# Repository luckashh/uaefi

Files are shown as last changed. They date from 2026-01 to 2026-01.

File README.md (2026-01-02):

# Ultra Affordable EFI

🟢[$175 base model rusEFI store](https://www.shop.rusefi.com/shop/p/uaefi-ultra-affordable-efi)🟢

## Community Support

🔴Community support ONLY 🔴 https://www.facebook.com/groups/rusEfi 🔴 [Discord](https://github.com/rusefi/rusefi/wiki/Discord)🔴 [Commercial Support](https://www.shop.rusefi.com/shop/p/details-about-rusefi-ecu-technical-support) 🔴

## Technical Details

Open Source KiCAD hardware powered by [Hellen-One](https://github.com/andreika-git/hellen-one)

Powered by [rusEFI firmware](https://github.com/rusefi/rusefi)

[User Documentation](https://github.com/rusefi/rusefi/wiki/uaEFI)





## MCU options

1mb of flash is _required_.

One day we shall try https://jlcpcb.com/partdetail/Stmicroelectronics-STM32F427VIT6%2FC57097#EC or https://jlcpcb.com/partdetail/Stmicroelectronics-STM32F437VIT7%2FC1338578#EC

## rusEFI Store

https://www.shop.rusefi.com/shop/p/uaefi-ultra-affordable-efi

## HOWTO JLCPCB

You would need three files from ``boards/uaefi-a/board`` folder to place your JLCPB Assembly order: gerber.zip BOM-JLC.csv and CPL.csv

### Q: having trouble with opening uaefi board project. library path seems ok, i do not know how to solve missing modules issue

A: missing modules are closed source. they are filled in by github magic
github magic combines gerbers and spits out a complete bom/pcl/new gerbers to upload to jlc/friends. See https://github.com/rusefi/hellen-one/tree/master?tab=readme-ov-file#tldr for more info

### Q: Magic modules? How do I see schematics of those?

A: https://github.com/rusefi/hellen-one has full documentation for each module

### Q: Something wrong with BOM?

A: Nope, that's normal nothing to worry about click 'Continue'.



### Q: how do I get more RAM for Lua?

A: fabricate with STM32F42xVI firmware would defect extra RAM and give you extra Lua. Once your script does not fit into STM32F42xVI it's F7 time or help us leverage F413.

### Q: I've place an order with JLCPCB and I see scary looking wrong orientation?

A: that's expected. See [boards/uaefi-c/board](boards/uaefi-c/board) ``Original*.png`` files and ``Produce*.png`` after JLCPCB manual review process.

## Bluetooth power issue fix

It was found that board with installed BT module may be affected by power issue.

During power on BT module consume too much inrush current on 3.3V line causing 3.3V drop below MCU reset hreshold. This may lead to unstable start or infinity reset loop.

To fix this please install additional capacitors to 5V and 3.3V powerlines.

Polarized electrolytic capacitors with at least 10V rating and extended temperature range are recommended. Tantalum and solid electrolytic capacitors are also suitable.

**Please carefully follow illustrated polarity.**

33..47uF should be added to 5V powerrail. [This](https://www.digikey.com/en/products/detail/w%C3%BCrth-elektronik/860020372004/5727028) or [this](https://www.digikey.com/en/products/detail/w%C3%BCrth-elektronik/860080372001/5727224) or [any of these](https://www.digikey.com/en/products/filter/aluminum-electrolytic-capacitors/58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).



And 220..470uF should be added to 3.3V powerrail. [This](https://www.digikey.com/en/products/detail/w%C3%BCrth-elektronik/860010273011/5726952) or [this](https://www.digikey.com/en/products/detail/w%C3%BCrth-elektronik/860020273011/5727148) or [any of these](https://www.digikey.com/en/products/filter/aluminum-electrolytic-capacitors/58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).



## HOWTO EGT chip

This board has a placeholder for MAX31855 (or MAX6675) termocouple-to-digital chip. **This chip is not populated by default!**

Screenshot from 2025-09-26 11-15-15

D8 is **optional** ESD protection and also is not populated by default. You need to solder U4 only, D8 is optional. All passive components are already populated.

**MAX31855** works without addtional modification.

For **MAX6675** connect EGT- to GNDA either on J2 "C" connector or just short C28 (replace with 0R).

Screenshot from 2025-09-26 11-19-41

## [EXPERIMENTAL] How to make MAX9924 work with low tooth count trigger wheel

In some cases user may need two VR inputs on UAEFI and both trigger wheels are low-tooth count.

In default configuration MAX9924 does not work with low count trigger wheels because of its "adaptive peak threshold" and its watchdog.

Screenshot from 2025-10-12 16-58-30

On UAEFI MAX9924 is configured in **A2 mode**.

Screenshot from 2025-10-12 16-59-49

**B mode** allow use of MAX9924 with low count trigger wheels. But external Bias and Thresholt voltages should be allpied. Both can be sources from UAEFI Discrete VR module.

List of modifications:
1. pin 6: ZERO_EN connect to VCC instead of GND.
2. pin 4: supply 2.5 V instead of GND
3. pin 8: EXT, supply external threshold voltage

Pins 4 and 6 needs to be lifted from PCB to be disconnected from GND. Pin 8 initially is not connected to any circuit.

Use hot air gun to de-solder whole chip. Then twist pins 4 and 6 up so both do not touch PCB. Then solder chip back to PCB

Now use thin wire to connect:
1. pin 6 to pin 10 of the same chip.
2. pin 4 to **Vref** at R769 + C754. See file:///home/work/rusefi/docs/uaefi-d-ibom.html for its locations
3. pin 8 to **thresh_high** at U756 pin 1. See file:///home/work/rusefi/docs/uaefi-d-ibom.html for its locations



Now MAX9924 VR input uses same threshold vs RPM settings that is set for Descrete VR input. And it is cabable to work with low tooth count trigger wheels without noise issues.

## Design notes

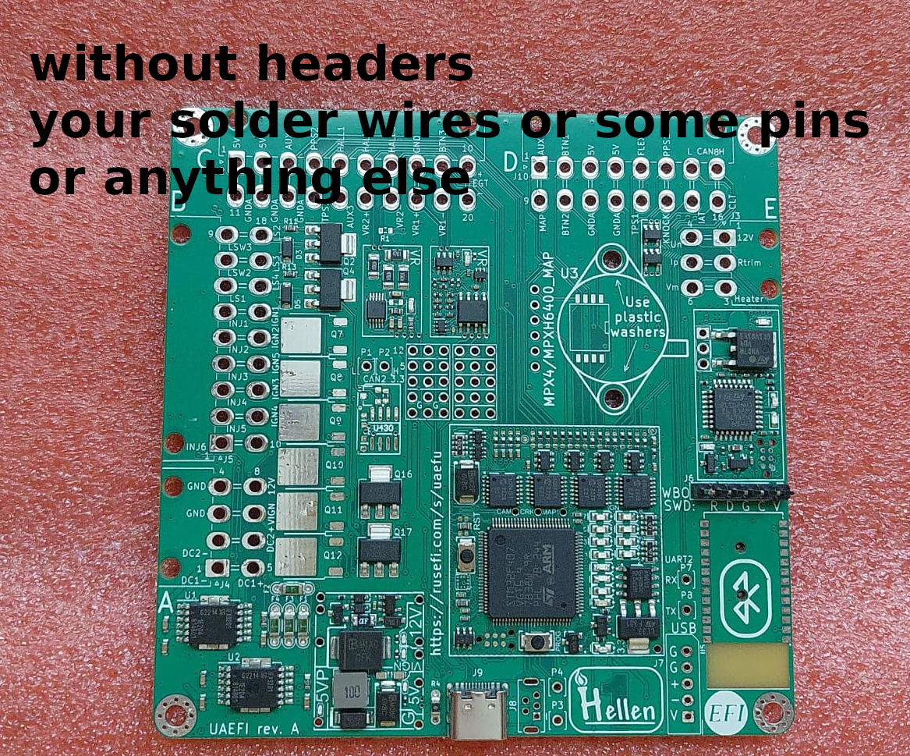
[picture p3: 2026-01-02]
docs/without-headers.png

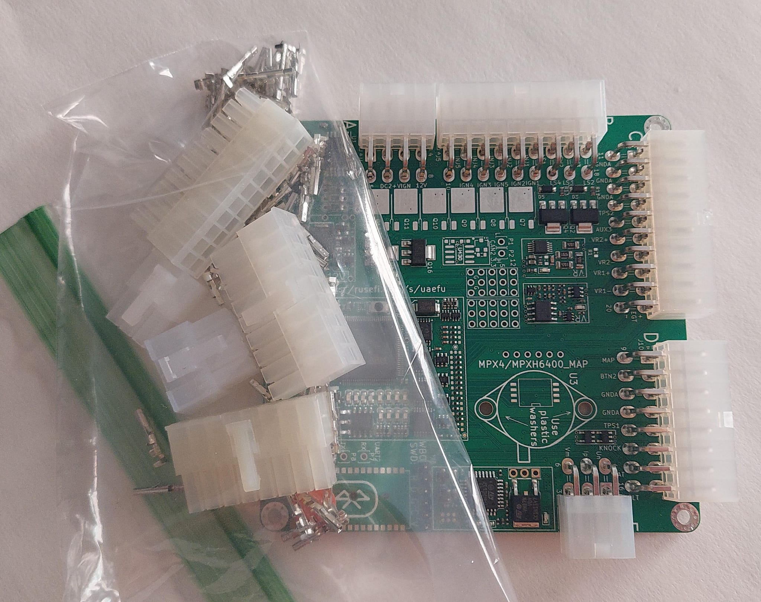
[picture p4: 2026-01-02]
docs/with-crimp-kit.jpg

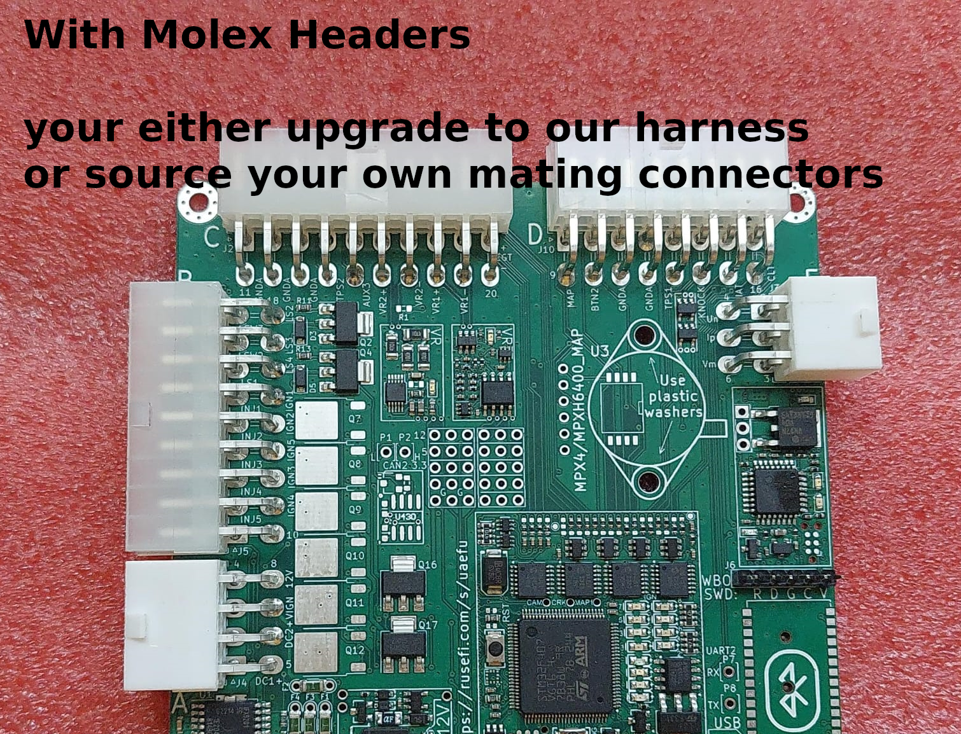
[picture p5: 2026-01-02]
docs/with-headers.png

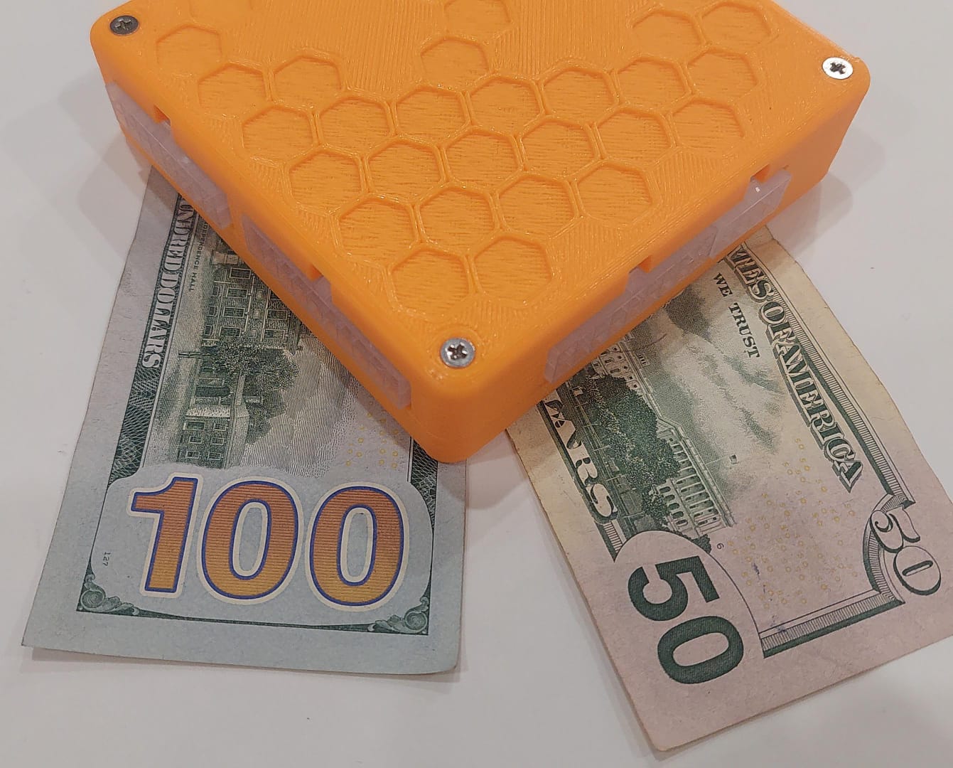
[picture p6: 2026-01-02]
docs/orange-150.jpg

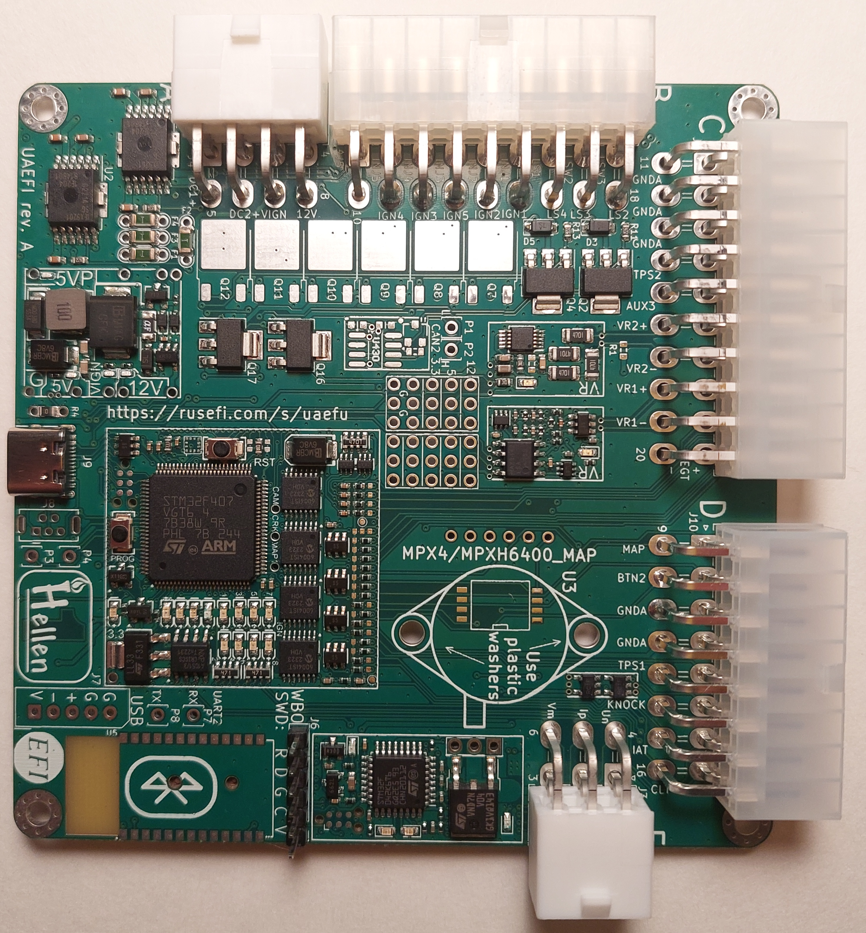
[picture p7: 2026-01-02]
docs/uaefi-a-top-high-res.jpg

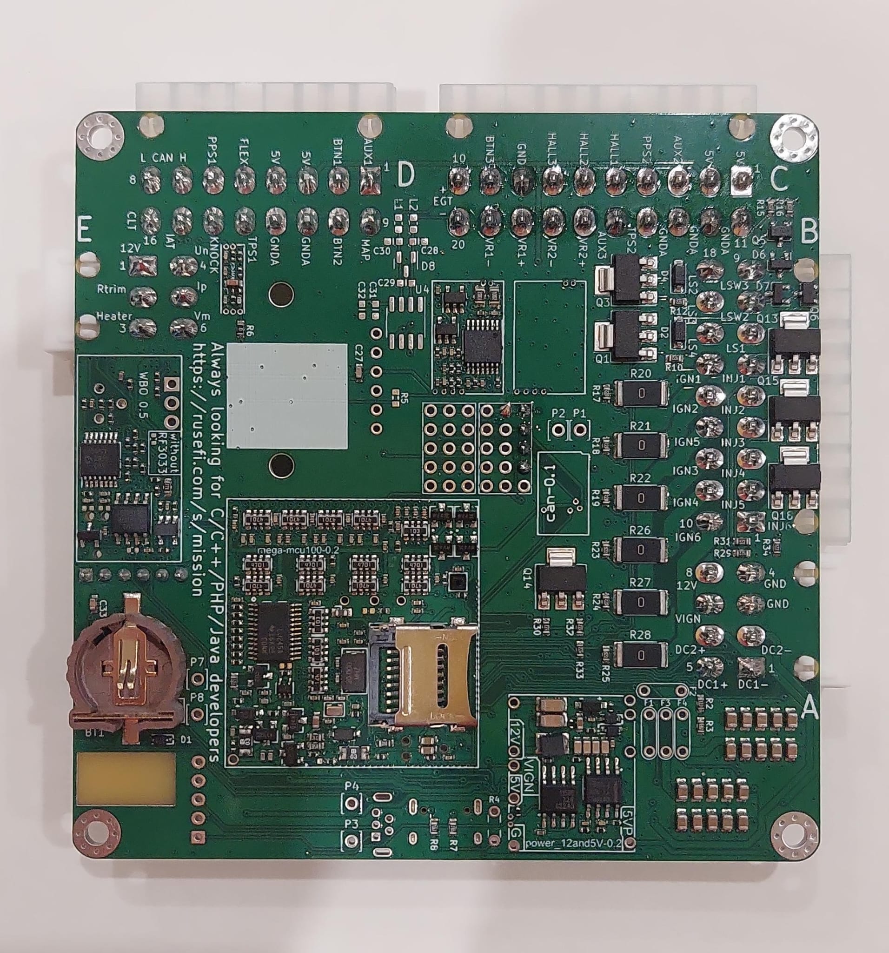
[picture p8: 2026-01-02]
docs/base-bottom.jpg

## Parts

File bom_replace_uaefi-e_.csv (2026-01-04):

# remove +5V pull-ups from SPI1, because we use it with +3.3v accelerometer
R103,
R105,
# remove jumper resistor connecting BOOT1 with A22 input line, because we use STM32F4
R131,
#CAN wakeup disabled, O2S input enabled
R145,
#PWR_EN not used as GPIO
R142,
# DC-DC Inductor
L421,"MWSA0503S-100MT","MWSA0503","C408412"
L420,"NLCV32T-2R2M-EF","L1210","C250227"
# fuses
F410,"nSMD050-24V","SMD1206","C70076"
# replacement not needed "F1,F2,F3,F4","5A","F1206","C553924"
# TLS115
U411,"TLS115B0EJXUMA1","PG-DSO-8","C3747428"
#MAX9142
U754,"TLV3202AIDR","SO8","C129325"
# cost reduction
U106,
# DNP BLUETOOTH JDY
U5,
# more proper part and shelf
"U1,U2","TLE9201SG","Infineon_PG-DSO-12-11","C2653438"
# EGT System restored
"U4","MAX31855KASA","SO-8","C50438"
"D8","MMSZ5231B","SOD-123","C13710"
"C603","33n","C0402","C106862"
#Knock capacitor
"C471","3.3n","C0402","C107028"
# max9924
U771,"MAX9924UAUB+T","MSOP10","C5145181"
# STM32F407VGT6 is very cheap
U105,"STM32F407VGT6","LQFP100","C12345"
# CAN2 restored
"U430","SIT1050T/E","SOIC-8","C12271"
"D430","PESD2CAN","SOT-23","C14986"
"R430","120","R0603","C22775"
"C430,C431","100n","C0603","C14663"
#20MHz crystal
# replacement not needed Y102,"TXM20M0002503LFBEO00T","SMD5032-2P","C362485"
#SD Card
J100,"TF-014-H16","SMD","C125814"
#board ID capacitor shortage
"C123,C133","1u","C0603","C14664"
R609,"61.9","R0603","C321964"
#VNLD5090
"U6,U7,U8,U9,U10,U11","VNLD5090","SO-8","C222209"
#mux
"U755,U756","WAS3157B-6","SOT-363","C213161"
#78 IGN buf switch to SN74LXCH8T245PWR
U103,"SN74LXCH8T245PWR","TSSOP-24","C2918963"
#79 RTC battery drain
D107,
# availability and cost reduction
J2,"5569-20A2","2x10P 2 4.2mm Female pin 4.2mm","C2845795"
J3,"5569-06A2","2x3P 2 4.2mm 4.2mm 3 Brass Push-Pull","C19188572"
J4,"5569-08A2","2x4P 2 Tin 4.2mm Female 4.2mm","C388760"
J5,"5569-18A2","2x9P 2 4.2mm Female 4.2mm 9 Right-Angle","C725776"
J10,"39301160","02x08_4.2mm","C5355564"
# Q1 Selection (Verified for 2026)
# ZXMS6005SGTA is the best cost/performance ratio for 2A loads.
# VNL5160 is not a direct drop-in replacement due to different pinout/logic.
"Q1","ZXMS6005SGTA","SOT-223","C174042"
# cost
"D411","PSM712-LF","SOT-23","C5180294"
#LEDs
"D106","YELLOW_LED","LED0603","C165983"
"D751,D771,D601,D104,D108","GREEN_LED","LED0603","C965804"
"D602,D105,D109,D110,D111,D112,D113,D114,D115,D116","BLUE_LED","LED0603","C497940"
"LED1, LED2, LED3, LED4","BLUE_LED","LED0402","C434447"
# same board ID as rev A for now!
#include hellen-one/board_id/generated/board_id_uaefi-a.csv
#include bom_pullups_uaefi-e.csv

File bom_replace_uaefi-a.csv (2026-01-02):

# remove +5V pull-ups from SPI1, because we use it with +3.3v accelerometer
R103,
R105,
# remove jumper resistor connecting BOOT1 with A22 input line, because we use STM32F4
R131,
#CAN wakeup disabled, O2S input enabled
R145,
#PWR_EN not used as GPIO
R142,
# DC-DC Inductor
L421,"MWSA0503S-100MT","MWSA0503","C408412"
# fuses
F410,"nSMD050-24V","SMD1206","C70076"
# TLS115
U411,"TLS115B0EJXUMA1","PG-DSO-8","C3743696"
# no software for accelerometer
U106,
# STM32F407VGT6 is very cheap
U105,"STM32F407VGT6","LQFP100","C12345"
#without CAN2
"C430,C431,D430,R430,U430",
#20MHz crystal
Y102,"TXM20M0002503LFBEO00T","SMD5032-2P","C362485"
#SD Card
J100,"TF-014-H16","SMD","C125814"
#board ID capacitor shortage
C133,"1u","C0603","C519559"
#mux
"U755,U756","WAS3157B-6","SOT-363","C213161"
#02x08 shortage
J10,"39301160","02x08_4.2mm","C5355564"
# Q1 options
# ZXMS6005SGTA C174042
# ZXMS6005DGTA C174045
# NCV8440ASTT3G C604063
# would VNL5160 work? would VNL5160 be the cheapest option?
#include hellen-one/board_id/generated/board_id_uaefi-a.csv
#include bom_pullups_uaefi-a.csv

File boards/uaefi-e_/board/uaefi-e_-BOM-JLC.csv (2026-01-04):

Comment | Designator | Footprint | LCSC Part #
CR1220 | BT1 | CR1220-2 | C70381
10u | C1, C2, C3, C4, C5, C6, C7, C8, C9, C10, C14, C15, C16, C17, C18, C19, C20, C21, C22, C23 | C0805 | C15850
100n | C11, C24, C27, C29, C31, C33, C772, C430, C431 | C0603 | C14663
10n | C12, C13, C25, C26, C28, C30 | C0603 | C57112
1u | C32 | C0603 | C15849
1N4148WS | D1, D410, D412, D413, D414 | SOD-323 | C2128
B5819W | D2, D3, D4, D5, D416, D417, D101 | SOD-123 | C8598
12H1500D | F1, F2, F3, F4 | PAD-1206-PAD | C182446
50mA | F5, F6, F7, F8, F9, F10 | Fuse_0603_1608Metric | C369141
Conn_01x06 | J6 | PinHeader_1x06_P2.54mm_Vertical | C37208
USB_C | J9 | USB_C | C2927038
470R@100MHz | L1, L2 | L_0603_1608Metric | C97853
33k | R2, R120 | R0603 | C4216
6.8k | R3 | R0603 | C23212
Jumper-Pad-Pad | R4 | PAD-0805-PAD | C17477
0 | R6 | R0603 | C21189
5.6k | R7, R8 | R0603 | C23189
4.7k | R9, R10, R11, R12, R13, R14, R15, R16, R29, R30, R31, R32, R33, R34 | R0603 | C23162
22 | R17, R18, R19, R23, R24, R25 | R0603 | C23345
0 | R20, R21, R22, R26, R27, R28 | R2512 | C25469
10k | R35, R36, R37, R752, R753 | R0805 | C17414
47u | C410, C412 | C1206 | C96123
100n | C411, C413, C420, C470, C228 | C0402 | C307331
1u | C414, C415, C755, C758, C761, C762, C763, C765, C766, C767, C600, C607, C609, C610, C611 | C0402 | C52923
10u | C421, C422, C423, C424, C425 | C0603 | C96446
47u | C426 | C0603 | C140782
4.7u | C427, C616 | C0603 | C19666
10n | C428, C756, C757, C760, C764, C768, C769, C203, C202, C201, C200, C214, C215, C225, C226, C227 | C0402 | C15195
220p | C429 | C0402 | C1530
BAS416 | D415 | SOD-323 | C968040
SMCJ30A | D418 | SMC | C310046
SS34 | D420 | SMA | C8678
P6SMB6.8CA | D421, D205 | SMB | C78395
MHT136UGCT | LED1, LED2, LED3, LED4 | LED0402 | C434447
6.8k | R410, R413 | R0402 | C25917
33k | R411, R424, R425, R474 | R0402 | C25779
1 | R420 | R0402 | C25086
10k | R421, R426, R427, R757, R762, R763, R767, R768, R604, R605, R613, R614, R618, R619, R625, R102, R107, R108, R109, R121, R127, R128, R141, R219 | R0402 | C25744
68k | R422, R760, R602, R603 | R0402 | C36871
12k | R423, R472, R754 | R0402 | C25752
4.7k | R428, R144, R202, R201, R124, R126, R132 | R0402 | C25900
MIC5205-3.3YM5 | U410 | SOT23-5 | C37970
LMR14020 | U420 | SOP8 | C187824
330p | C472 | C0402 | C13533
47p | C473 | C0402 | C1567
680p | C474 | C0603 | C1630
470k | R470 | R0402 | C25790
100k | R471, R473, R755, R756, R758, R759, R615, R621 | R0402 | C25741
LMV321IDBVR | U470, U471 | SOT23-5 | C7972
1n | C751, C135, C139, C141, C142, C211, C209, C208, C212, C213, C210, C143, C144, C145, C146 | C0402 | C1523
470n | C752 | C0402 | C47339
100n | C753, C754, C759, C601, C602, C605, C608, C612, C613, C614, C615, C617, C618, C100, C101, C105, C108, C111, C112, C113, C119, C120, C122, C124, C126, C127, C130, C134, C147, C180, C185, C190, C195, C220, C221, C222 | C0402 | C1525
2.2k | R751, R122, R123, R146, R147 | R0402 | C25879
10 | R761, R764, R769, R606, R110, R111, R112, R113, R114, R115, R116, R117 | R0402 | C25077
1k | R765, R766, R600, R601, R616, R617, R622, R626, R627, R628 | R0402 | C11702
SRV05-4-P-T7 | U751, D102, D200, D202, D203, D206 | SOT23-6 | C85364
74AHC1G02 | U752, U757 | SOT23-5 | C7463
MCP6004 | U753, U600, U180, U185, U190, U195 | TSSOP14 | C50282
1n | C771 | C0603 | C1588
22u | C773 | C0603 | C59461
4.7k | R771, R772, R773, R774 | R1206 | C17936
10k | R776, R777, R134 | R0603 | C25804
LED-RED-0603 | D600, D603, D103 | LED-0603 | C2286
PESD1CAN | D604, D100 | SOT-23 | C343993
VND7NV04TR-E | Q600 | DPAK | C155605
22k | R607 | R0402 | C25768
47 | R608 | R0402 | C25118
20k | R610, R611, R612 | R0402 | C25765
27k | R620, R623 | R0402 | C25771
3.3k | R624 | R0402 | C25890
AD8628 | U601 | TSOT23-5 | C29309
STM32F042K6Tx | U602 | LQFP32 | C69216
REF3033 | U603, U102 | SOT-23 | C36658
XC6206P332MR | U604 | SOT-23 | C5446
TJA1051T/3/1J | U605, U100 | SO8 | C38695
SN74LVC1G06DCKR | U110 | SC-70-5 | C7828
SMD1206B035TF/16 | F100, F101 | R1206 | C269114
LPS22HBTR | U107 | HLGA-10L | C94049
LDL1117S33R | U101 | SOT-223 | C435835
BTN | S100, S101 | SMD-2_2.9x3.9x1.7 | C115357
BLM18AG601SN1D | L100 | L0603 | C19330
BAT54S | VD100, VD101, VD102, VD103 | SOT-23 | C47546
AO3401A | Q100, Q102 | SOT-23 | C15127
AO3400A | Q101, Q103 | SOT-23 | C20917
510 | R254, R255, R256, R258 | R0402 | C25123
470 | R101, R118, R119 | R0603-4 | C25510
120 | R100 | R0603 | C22787
100 | R104, R106, R430 | R0603 | C22775
74LVC2G17GW,125 | U108, U109 | SOT-363 | C80500
32.768 kHz | Y101 | SMD2012 | C99009
20 MHz | Y102 | SMD5032 | C112566
18p | C132, C136 | C0402 | C1549
12p | C115, C116 | C0402 | C1547
10k | R129, R130, R140 | R0603-4 | C29718
5.1k | R195 | R0402 | C25905
4.7u | C102, C103, C104, C106, C107, C137, C138, C140 | C0402 | C23733
4.7k | R125, R180, R181, R185, R186, R190, R191, R196, R197, R200, R218, R227, R245 | R0603-4 | C66697
2.2u | C114, C131, C223, C224, C229 | C0402 | C12530
0 | R143, R148 | R0402 | C17168
MWSA0503S-100MT | L421 | MWSA0503 | C408412
NLCV32T-2R2M-EF | L420 | L1210 | C250227
nSMD050-24V | F410 | SMD1206 | C70076
TLS115B0EJXUMA1 | U411 | PG-DSO-8 | C3747428
TLV3202AIDR | U754 | SO8 | C129325
TLE9201SG | U1, U2 | Infineon_PG-DSO-12-11 | C2653438
MAX31855KASA | U4 | SO-8 | C50438
MMSZ5231B | D8 | SOD-123 | C13710
33n | C603 | C0402 | C106862
3.3n | C471 | C0402 | C107028
MAX9924UAUB+T | U771 | MSOP10 | C5145181
STM32F407VGT6 | U105 | LQFP100 | C12345
SIT1050T/E | U430 | SOIC-8 | C12271
PESD2CAN | D430 | SOT-23 | C14986
TF-014-H16 | J100 | SMD | C125814
1u | C123, C133 | C0603 | C14664
61.9 | R609 | R0603 | C321964
VNLD5090 | U6, U7, U8, U9, U10, U11 | SO-8 | C222209
WAS3157B-6 | U755, U756 | SOT-363 | C213161
SN74LXCH8T245PWR | U103 | TSSOP-24 | C2918963
5569-20A2 | J2 | 2x10P 2 4.2mm Female pin 4.2mm | C2845795
5569-06A2 | J3 | 2x3P 2 4.2mm 4.2mm 3 Brass Push-Pull | C19188572
5569-08A2 | J4 | 2x4P 2 Tin 4.2mm Female 4.2mm | C388760
5569-18A2 | J5 | 2x9P 2 4.2mm Female 4.2mm 9 Right-Angle | C725776
39301160 | J10 | 02x08_4.2mm | C5355564
ZXMS6005SGTA | Q1 | SOT-223 | C174042
PSM712-LF | D411 | SOT-23 | C5180294
YELLOW_LED | D106 | LED0603 | C165983
GREEN_LED | D751, D771, D601, D104, D108 | LED0603 | C965804
BLUE_LED | D602, D105, D109, D110, D111, D112, D113, D114, D115, D116 | LED0603 | C497940
750 | R133 | R0603 | C23241
680k | R222, R220, R208, R207, R234, R235, R232, R233, R250, R251, R252, R225, R135 | R0402 | C4131

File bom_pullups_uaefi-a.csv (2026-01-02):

#CRANK BUTTON1: UP 10k 100n
R222 | 10k | R0402 | C25744
R226
C211 | 100n | C0402 | C307331
#CAM BUTTON2: UP 10k 100n
R220 | 10k | R0402 | C25744
R224
C209 | 100n | C0402 | C307331
#VSS FLEX: UP 10k 1n
R219 | 10k | R0402 | C25744
R223
C208 | 1n | C0402 | C1523
#TPS TPS1: DOWN 680k 10n
R204
R208 | 680k | R0402 | C163456
C203 | 10n | C0402 | C15195
#PPS PPS1: DOWN 680k 10n
R203
R207 | 680k | R0402 | C163456
C202 | 10n | C0402 | C15195
#IAT IAT: UP 4.7k 10n
R202 | 4.7k | R0402 | C25900
R206
C201 | 10n | C0402 | C15195
#CLT CLT: UP 4.7k 10n
R201 | 4.7k | R0402 | C25900
R205
C200 | 10n | C0402 | C15195
#O2S AUX1: DOWN 680k 10n
R230
R234 | 680k | R0402 | C163456
C214 | 10n | C0402 | C15195
#O2S2 AUX2: DOWN 680k 10n
R231
R235 | 680k | R0402 | C163456
C215 | 10n | C0402 | C15195
#MAP1 MAP: DOWN 680k 1n
R228
R232 | 680k | R0402 | C163456
C212 | 1n | C0402 | C1523
#MAP2 INTERNAL_MAP: DOWN 680k 1n
R229
R233 | 680k | R0402 | C163456
C213 | 1n | C0402 | C1523
#AUX1 TPS2: DOWN 680k 10n
R246
R250 | 680k | R0402 | C163456
C225 | 10n | C0402 | C15195
#AUX2 PPS2: DOWN 680k 10n
R247
R251 | 680k | R0402 | C163456
C226 | 10n | C0402 | C15195
#AUX3 AUX3: DOWN 680k 10n
R248
R252 | 680k | R0402 | C163456
C227 | 10n | C0402 | C15195
#AUX4 VMAIN: DOWN DNP 100n
R249
R253
C228 | 100n | C0402 | C307331
#KNOCK KNOCK: DOWN 680k 1n
R221
R225 | 680k | R0402 | C163456
C210 | 1n | C0402 | C1523
#D1 HALL1: UP 4.7k 1n
R124 | 4.7k | R0402 | C25900
R136
C143 | 1n | C0402 | C1523
#D2 HALL2: UP 4.7k 1n
R126 | 4.7k | R0402 | C25900
R137
C144 | 1n | C0402 | C1523
#D3 HALL3: UP 4.7k 1n
R132 | 4.7k | R0402 | C25900
R138
C145 | 1n | C0402 | C1523
#D4 BUTTON3: UP 10k 100n
R135 | 10k | R0402 | C25744
R139
C146 | 100n | C0402 | C307331

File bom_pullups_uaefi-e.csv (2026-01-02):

#CRANK BUTTON1: UP 680k 1n
R222 | 680k | R0402 | C4131
R226
C211 | 1n | C0402 | C1523
#CAM BUTTON2: UP 680k 1n
R220 | 680k | R0402 | C4131
R224
C209 | 1n | C0402 | C1523
#VSS FLEX: UP 10k 1n
R219 | 10k | R0402 | C25744
R223
C208 | 1n | C0402 | C1523
#TPS TPS1: DOWN 680k 10n
R204
R208 | 680k | R0402 | C4131
C203 | 10n | C0402 | C15195
#PPS PPS1: DOWN 680k 10n
R203
R207 | 680k | R0402 | C4131
C202 | 10n | C0402 | C15195
#IAT IAT: UP 4.7k 10n
R202 | 4.7k | R0402 | C25900
R206
C201 | 10n | C0402 | C15195
#CLT CLT: UP 4.7k 10n
R201 | 4.7k | R0402 | C25900
R205
C200 | 10n | C0402 | C15195
#O2S AUX1: DOWN 680k 10n
R230
R234 | 680k | R0402 | C4131
C214 | 10n | C0402 | C15195
#O2S2 AUX2: DOWN 680k 10n
R231
R235 | 680k | R0402 | C4131
C215 | 10n | C0402 | C15195
#MAP1 MAP: DOWN 680k 1n
R228
R232 | 680k | R0402 | C4131
C212 | 1n | C0402 | C1523
#MAP2 INTERNAL_MAP: DOWN 680k 1n
R229
R233 | 680k | R0402 | C4131
C213 | 1n | C0402 | C1523
#AUX1 TPS2: DOWN 680k 10n
R246
R250 | 680k | R0402 | C4131
C225 | 10n | C0402 | C15195
#AUX2 PPS2: DOWN 680k 10n
R247
R251 | 680k | R0402 | C4131
C226 | 10n | C0402 | C15195
#AUX3 AUX3: DOWN 680k 10n
R248
R252 | 680k | R0402 | C4131
C227 | 10n | C0402 | C15195
#AUX4 VMAIN: DOWN DNP 100n
R249
R253
C228 | 100n | C0402 | C307331
#KNOCK KNOCK: DOWN 680k 1n
R221
R225 | 680k | R0402 | C4131
C210 | 1n | C0402 | C1523
#D1 HALL1: UP 4.7k 1n
R124 | 4.7k | R0402 | C25900
R136
C143 | 1n | C0402 | C1523
#D2 HALL2: UP 4.7k 1n
R126 | 4.7k | R0402 | C25900
R137
C144 | 1n | C0402 | C1523
#D3 HALL3: UP 4.7k 1n
R132 | 4.7k | R0402 | C25900
R138
C145 | 1n | C0402 | C1523
#D4 BUTTON3: UP 680k 1n
R135 | 680k | R0402 | C4131
R139
C146 | 1n | C0402 | C1523

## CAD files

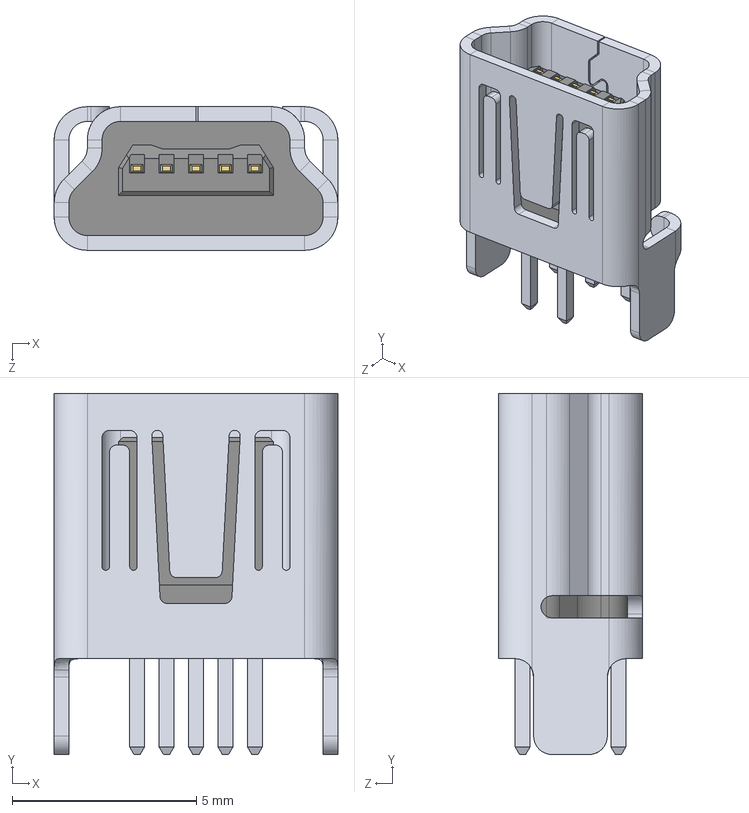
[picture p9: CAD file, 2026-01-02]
3D models/User Library-UE25BE5510H.STEP
7.70 x 9.80 x 3.90 mm

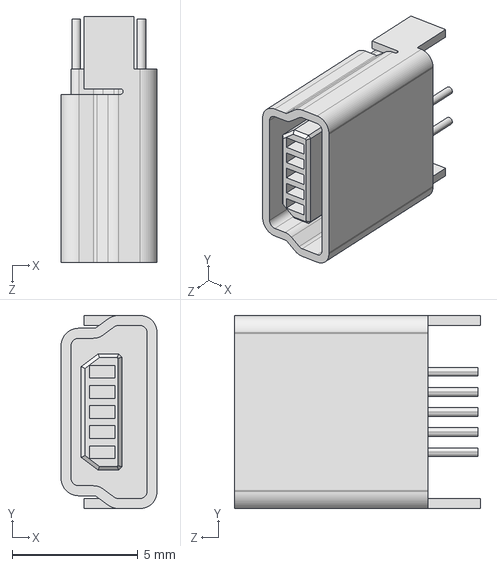
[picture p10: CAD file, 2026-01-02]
3D models/User Library-USB-B-Vert-MINI.STEP
3.83 x 7.69 x 9.80 mm

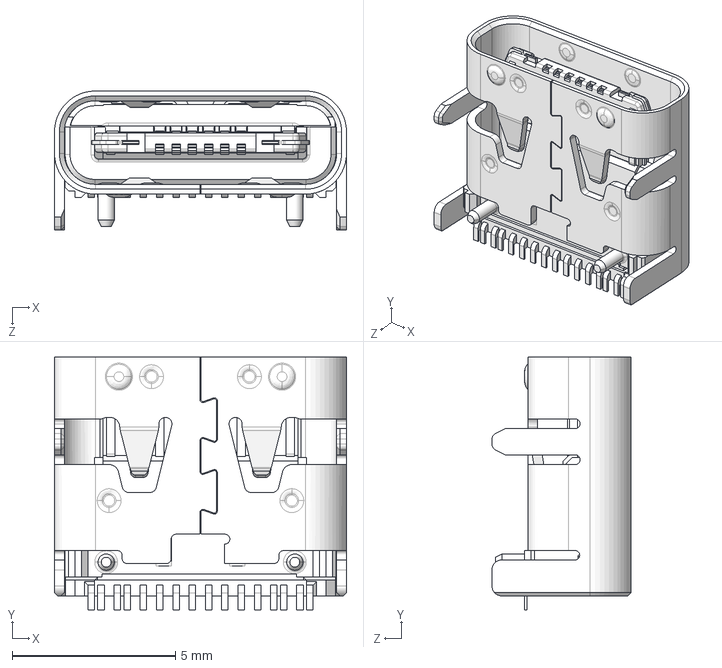
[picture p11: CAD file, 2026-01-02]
3D models/User Library-USB - C.STEP
8.95 x 7.75 x 4.26 mm

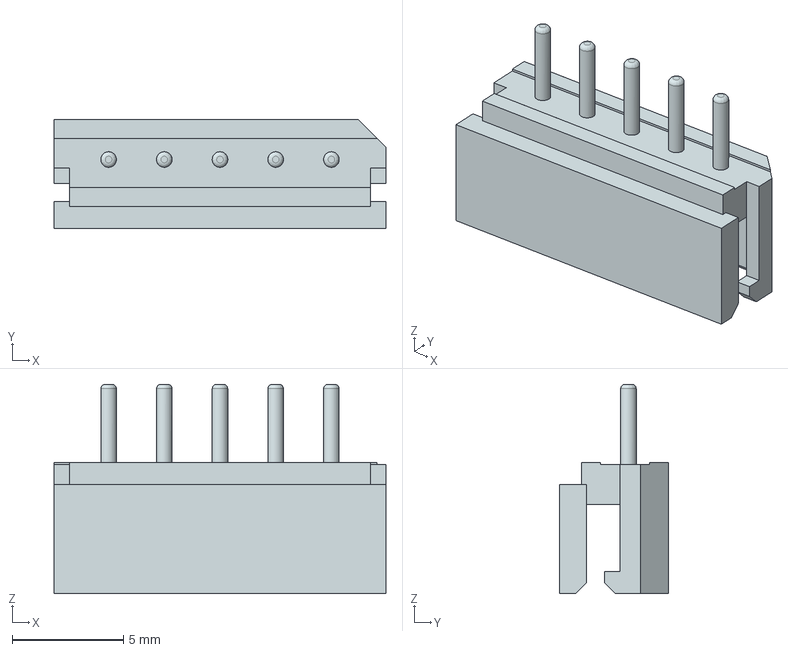
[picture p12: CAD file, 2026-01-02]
3D models/022035055.stp
14.9 x 4.90 x 9.40 mm

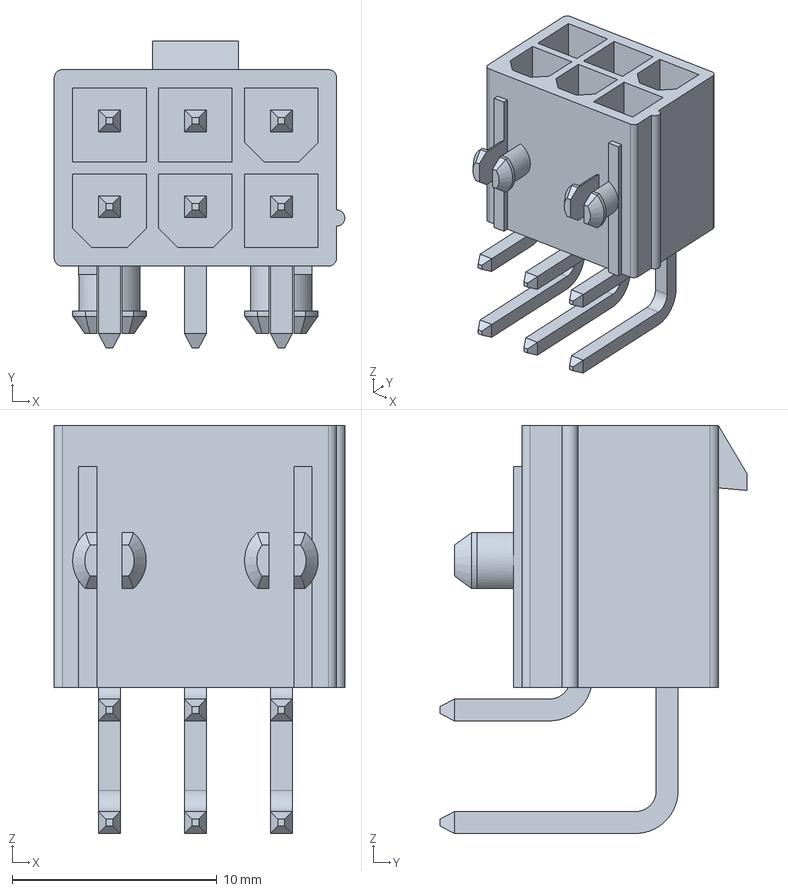
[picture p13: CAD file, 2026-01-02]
3D models/039301060.stp
14.2 x 15.0 x 19.9 mm

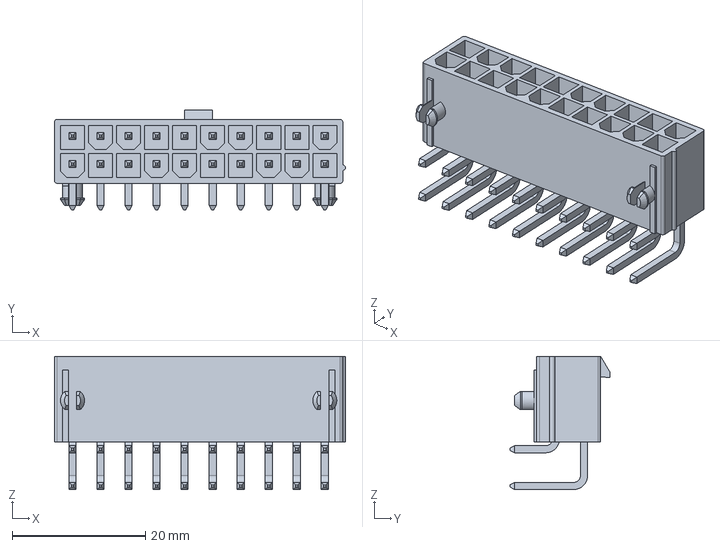
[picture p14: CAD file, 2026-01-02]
3D models/039301200.stp
43.6 x 15.0 x 19.9 mm

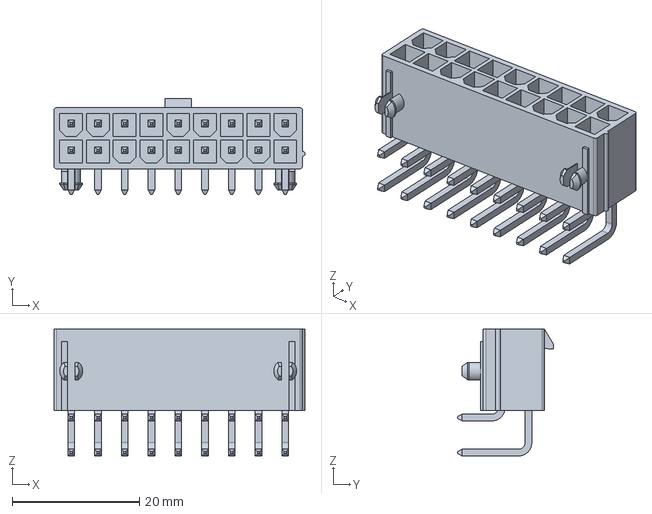
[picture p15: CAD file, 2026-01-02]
3D models/039301180.stp
39.4 x 15.0 x 19.9 mm

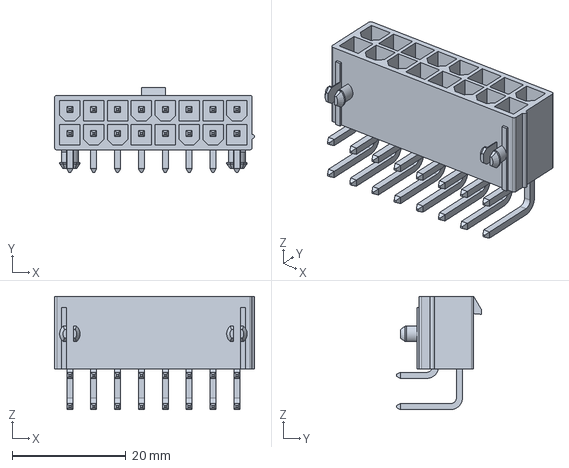
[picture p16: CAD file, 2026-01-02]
3D models/039301160.stp
35.2 x 15.0 x 19.9 mm

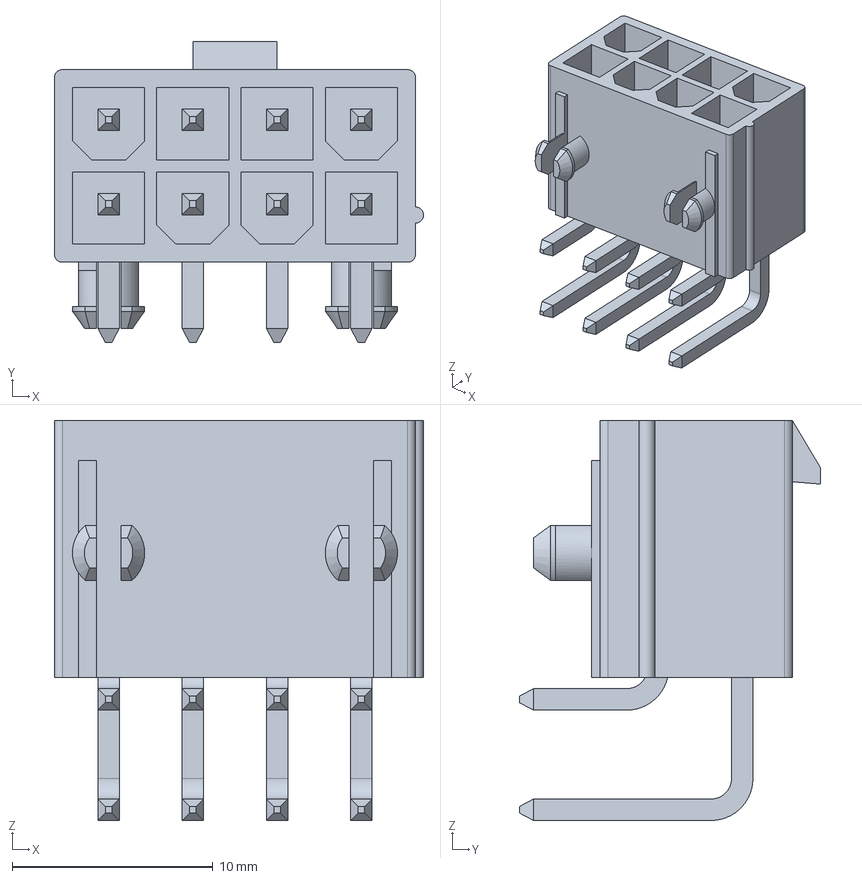
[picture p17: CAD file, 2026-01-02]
3D models/039301080.stp
18.4 x 15.0 x 19.9 mm

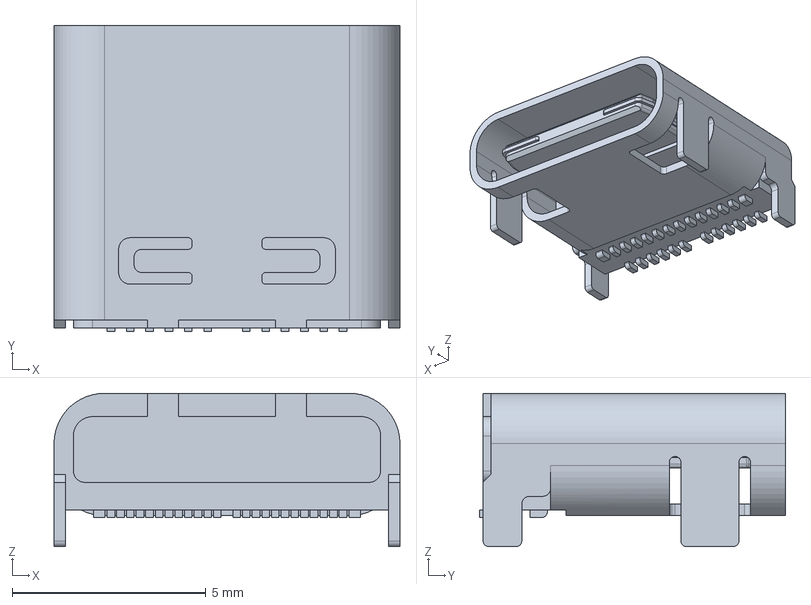
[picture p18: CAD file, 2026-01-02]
3D models/1054500101.stp
8.94 x 7.90 x 3.96 mm

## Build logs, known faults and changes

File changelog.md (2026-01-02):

# rev E

* power supply fix for RTC
* https://github.com/rusefi/uaefi/issues?q=state%3Aopen%20label%3A%22rev-E%22

# rev D

August 2024

* logic analyzer hookup points for both VRs #66
* minor silkscreen improvements https://github.com/rusefi/uaefi/issues?q=label%3Arev-D+is%3Aclosed

# rev C

Apr 2024

* pad for resistor between VR lines
* a few silkscreen corrections
* full list https://github.com/rusefi/uaefi/issues?q=label%3Arev-C+is%3Aclosed

# rev B

Feb 2024

* [over-current protection on all low side outputs](https://github.com/rusefi/uaefi/issues/44)
* [over-current protection on ignition outputs](https://github.com/rusefi/uaefi/issues/42)
* 0805 button input pull-up/pull-downs added
* button inputs changed from 10K PU to 680K PD https://github.com/rusefi/uaefi/issues/36
* minor cosmetic https://github.com/rusefi/uaefi/labels/rev-B

# rev A

Dec 2023

It works it's great!

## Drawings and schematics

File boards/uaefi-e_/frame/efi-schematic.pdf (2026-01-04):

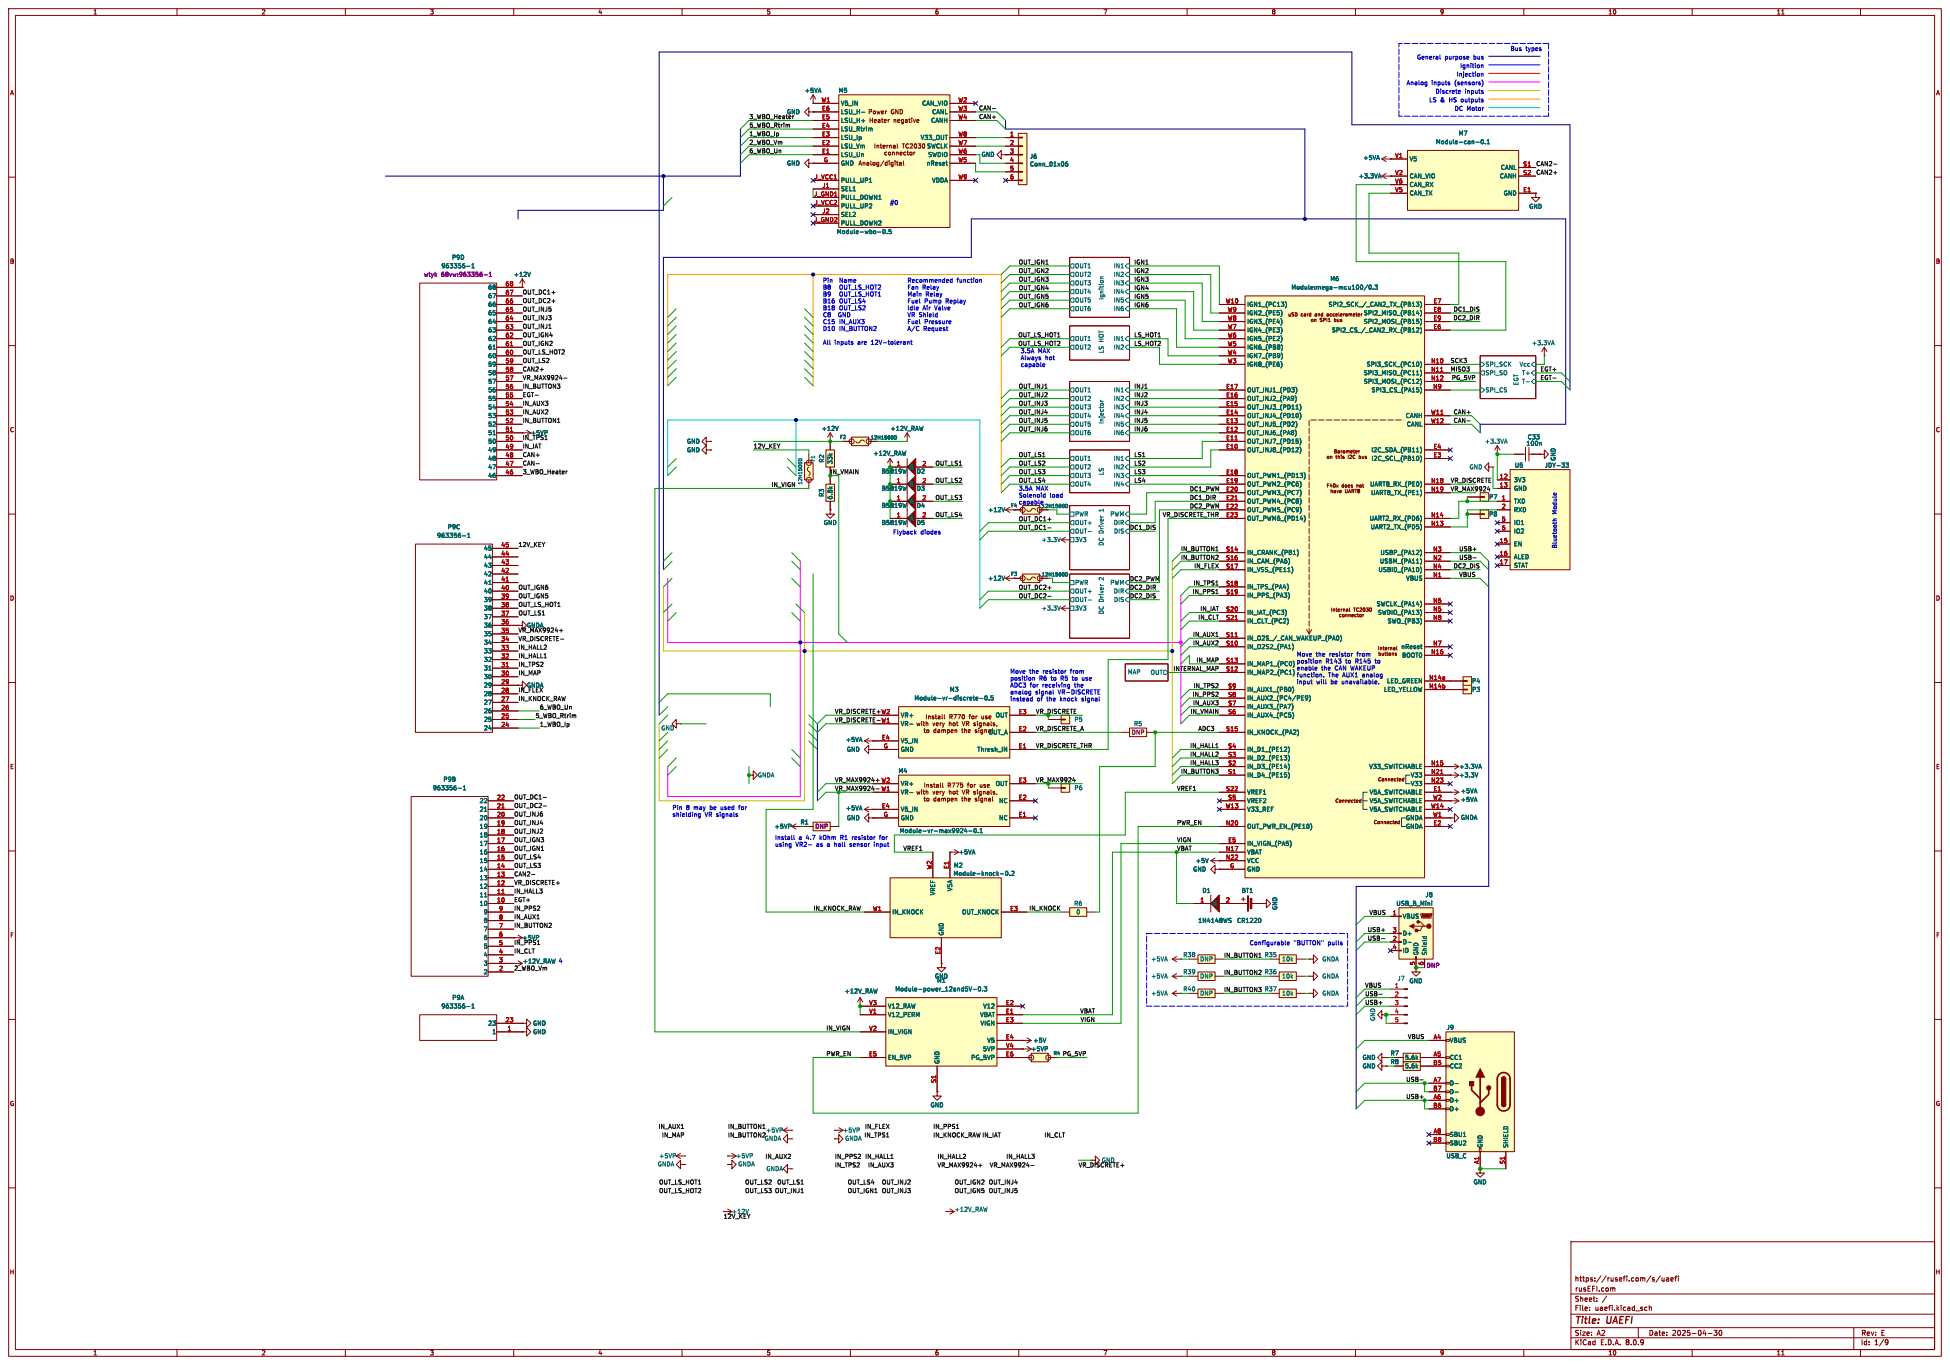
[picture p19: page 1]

Analog/digital Heater negative Power GND

enable the CAN WAKEUP
input will be unavailable.

analog signal VR-DISCRETE
instead of the knock signal

https://rusefi.com/s/uaefi

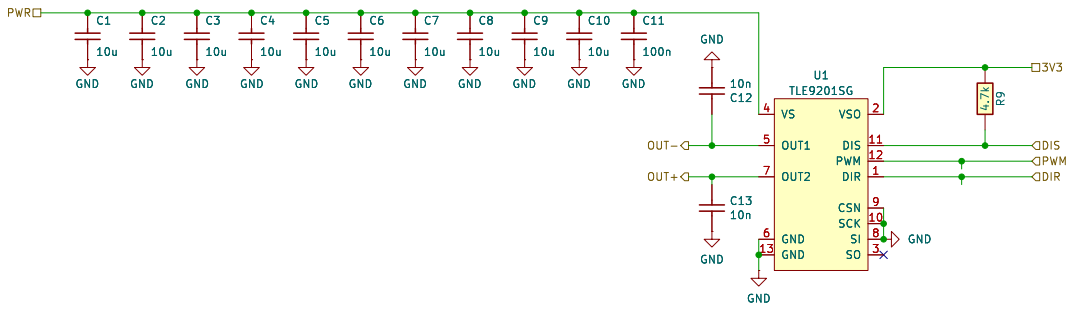
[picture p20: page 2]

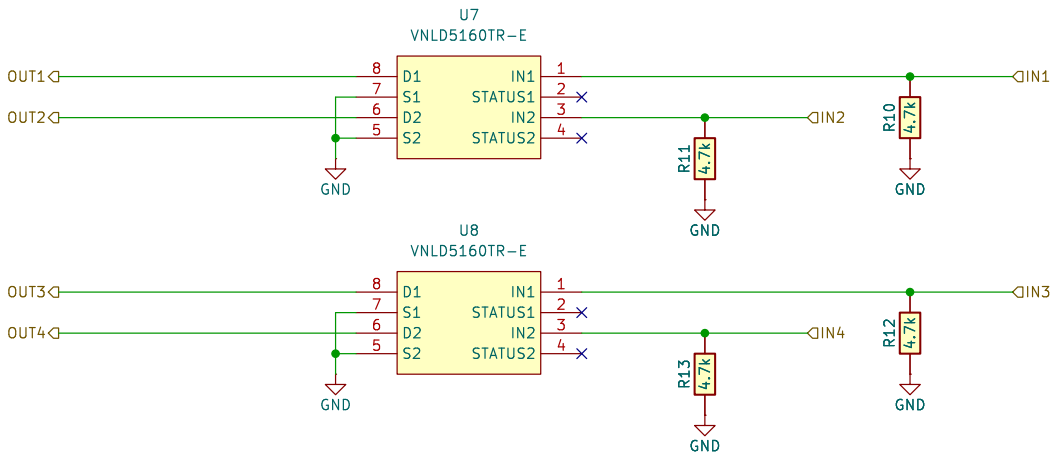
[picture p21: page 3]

Id: 3/9 Title: UAEFI File: LS4.kicad_sch Sheet: /LS/ rusEFI.com

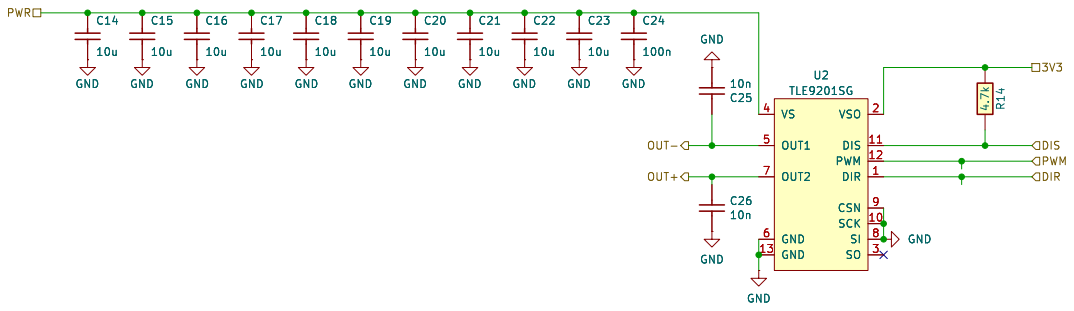
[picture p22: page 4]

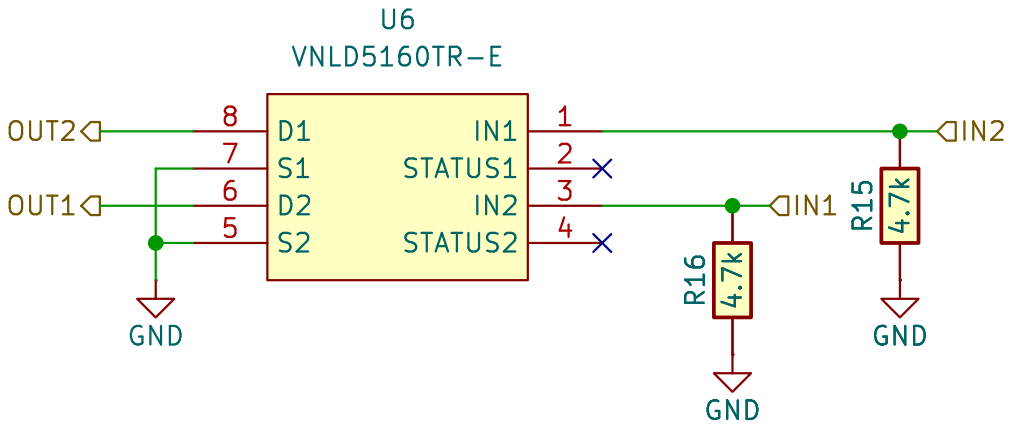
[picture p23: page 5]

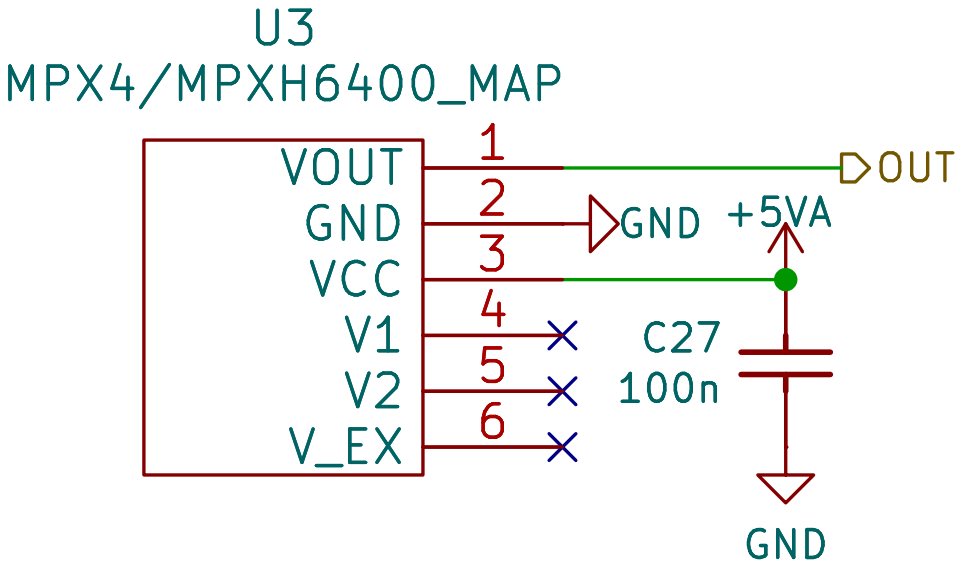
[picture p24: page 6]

Id: 8/9 Title: UAEFI File: MAP.kicad_sch Sheet: /MAP/ rusEFI.com

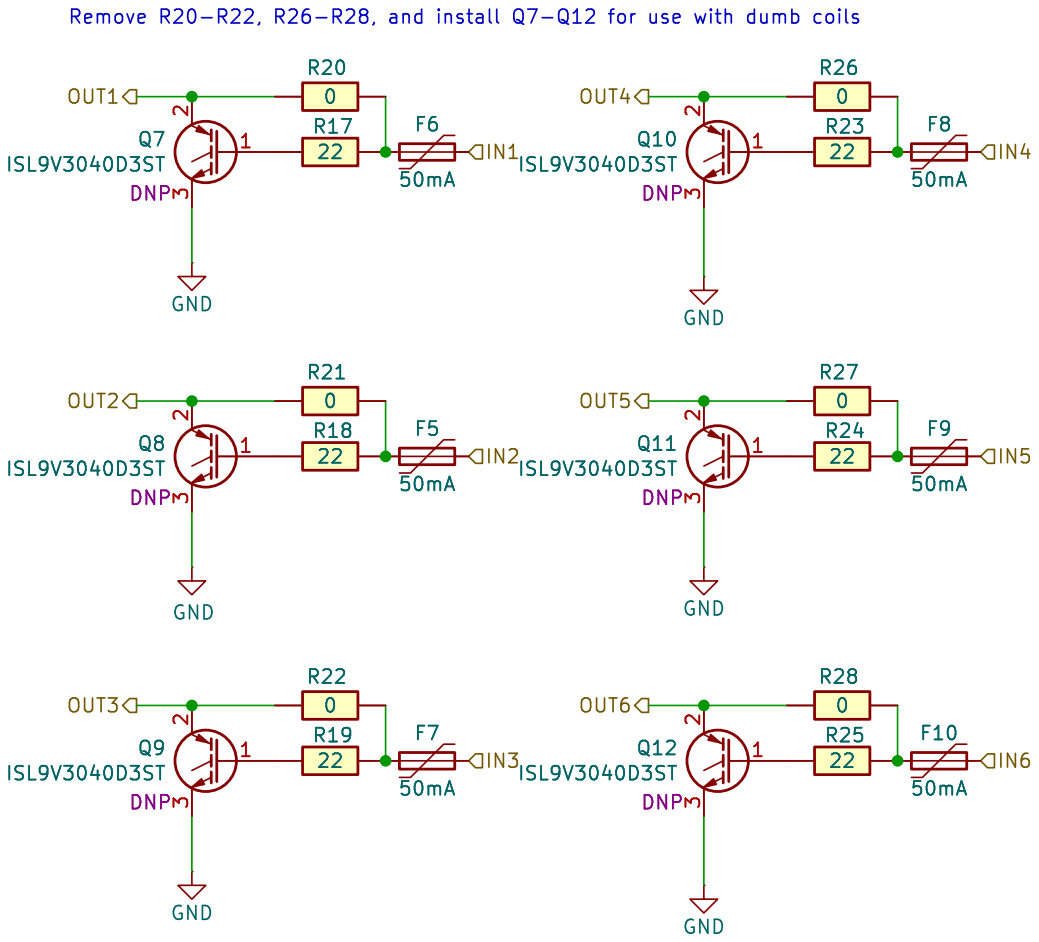
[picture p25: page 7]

Id: 9/9 Title: UAEFI File: IGN6.kicad_sch Sheet: /Ignition/ rusEFI.com

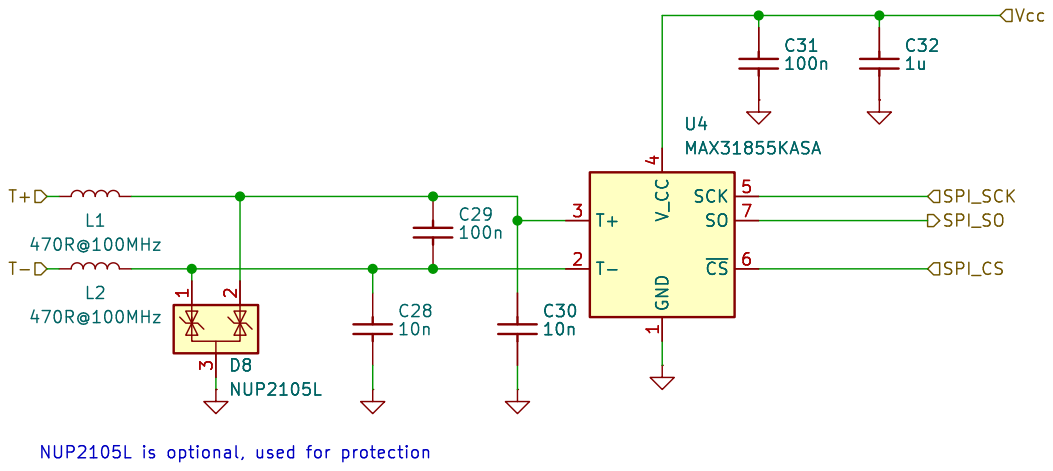
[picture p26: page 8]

Id: 9/9 Title: UAEFI File: egt.kicad_sch Sheet: /EGT/ rusEFI.com GND

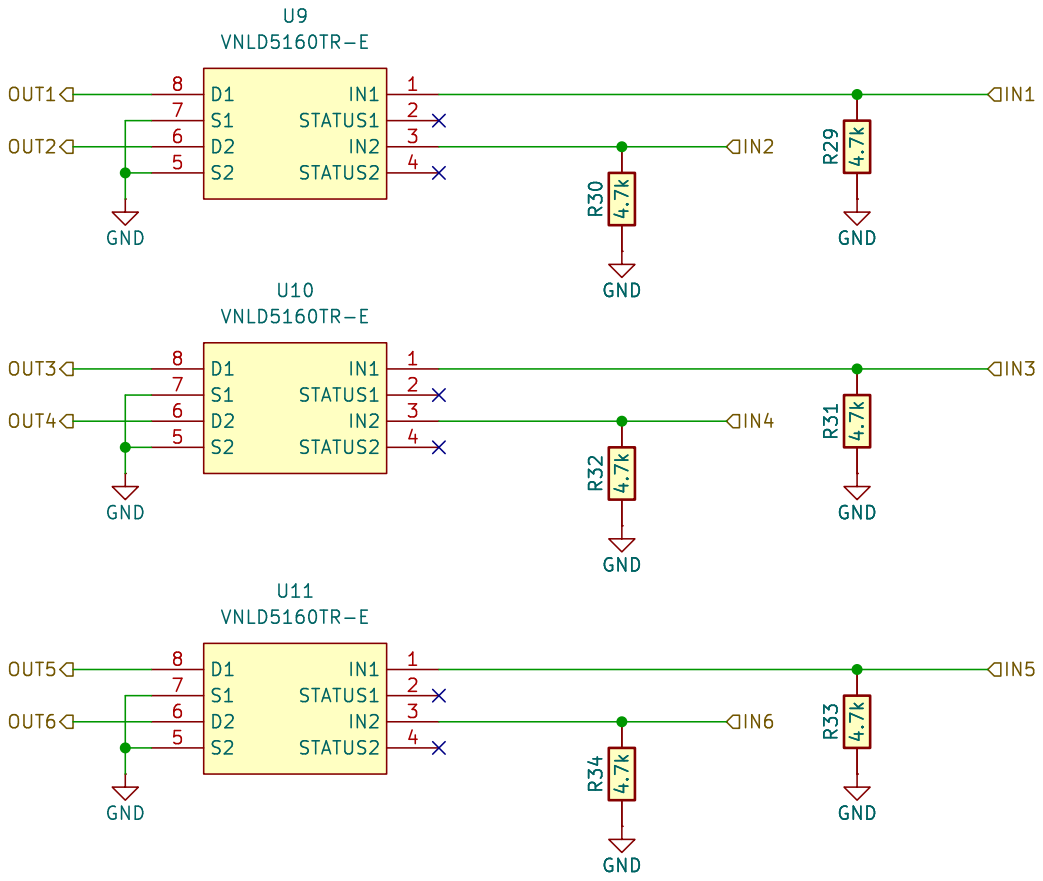
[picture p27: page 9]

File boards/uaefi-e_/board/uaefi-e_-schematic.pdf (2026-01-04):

# +3.3VA GND

nReset | W5 SWDIO | W6 SWCLK | W7 V33_OUT | W8 VDDA | W9 M5 Module-wbo-0.5 | +12V_RAW


Analog/digital Heater negative Power GND

enable the CAN WAKEUP
input will be unavailable.

analog signal VR-DISCRETE
instead of the knock signal

https://rusefi.com/s/uaefi


D Date: 2025-04-30 KiCad; E.D.A. 8.0.9 Size: A4; Rev:; GND GND; GND R¹² 4.7k R¹¹ 4.7k GND GND; R¹³ 4.7k; 1 STATUS1; 3 STATUS2; U7 VNLD5160TR-E; U8 VNLD5160TR-E; R¹⁰ 4.7k GND; IN2 OUT1; IN4 OUT3 OUT2 OUT4; R¹⁰ 4.7k GND GND R¹³ 4.7k GND R¹¹ 4.7k; R¹² 4.7k GND

Id: 3/9 Title: UAEFI File: LS4.kicad_sch Sheet: /LS/ rusEFI.com

D Date: 2025-04-30 KiCad; E.D.A. 8.0.9 Size: A4; Rev:; Id: 6/9 Title: UAEFI File: LS_HOT.kicad_sch Sheet: /LS; HOT/ rusEFI.com; GND R¹⁶ 4.7k GND; R¹⁵ 4.7k; 1 STATUS1; 3 STATUS2; U6 VNLD5160TR-E GND; IN2 OUT1 OUT2; R¹⁵ 4.7k GND R¹⁶ 4.7k; GND

D Date: 2025-04-30 KiCad; E.D.A. 8.0.9 Size: A4; Rev:; VOUT; 1 GND; 2 VCC; 6 U3 MPX4/MPXH6400_MAP; GND GND; OUT U3 MPX4/MPXH6400_MAP

Id: 8/9 Title: UAEFI File: MAP.kicad_sch Sheet: /MAP/ rusEFI.com


Id: 9/9 Title: UAEFI File: IGN6.kicad_sch Sheet: /Ignition/ rusEFI.com


Id: 9/9 Title: UAEFI File: egt.kicad_sch Sheet: /EGT/ rusEFI.com GND

6 ABCD; ABCD Date: 2025-04-30 KiCad; E.D.A. 8.0.9 Size: A4; Rev:; Id: 10/9 Title: UAEFI File: INJ6.kicad_sch Sheet: /Injector/ rusEFI.comR³³ 4.7k GND R³⁴ 4.7k GND GND R³² 4.7k; GND R³¹ 4.7k R³⁰ 4.7k GND; R²⁹ 4.7k GND; 1 STATUS1; 3 STATUS2; U9 VNLD5160TR-E GND GND; U11 VNLD5160TR-E GND; U10 VNLD5160TR-E OUT6; IN5 OUT4 OUT3 OUT5 OUT2 OUT1; GND R³⁰ 4.7k; R³¹ 4.7k GND R³² 4.7k GND GND R³⁴ 4.7k; GND R²⁹ 4.7k GND R³³ 4.7k

Hellen One : Power-Module interface

Reverse polarity and overvoltage protection
F410 V12_RAW

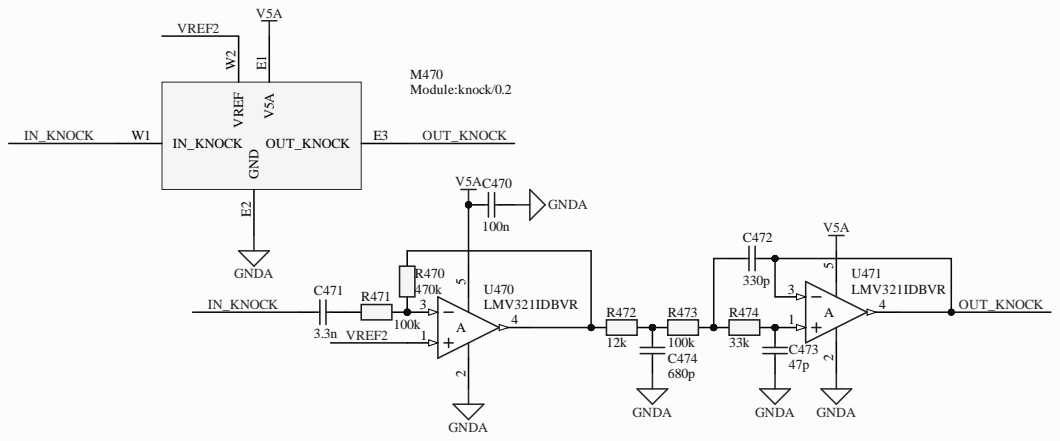
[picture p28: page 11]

# 6 U751 GND

1u R761

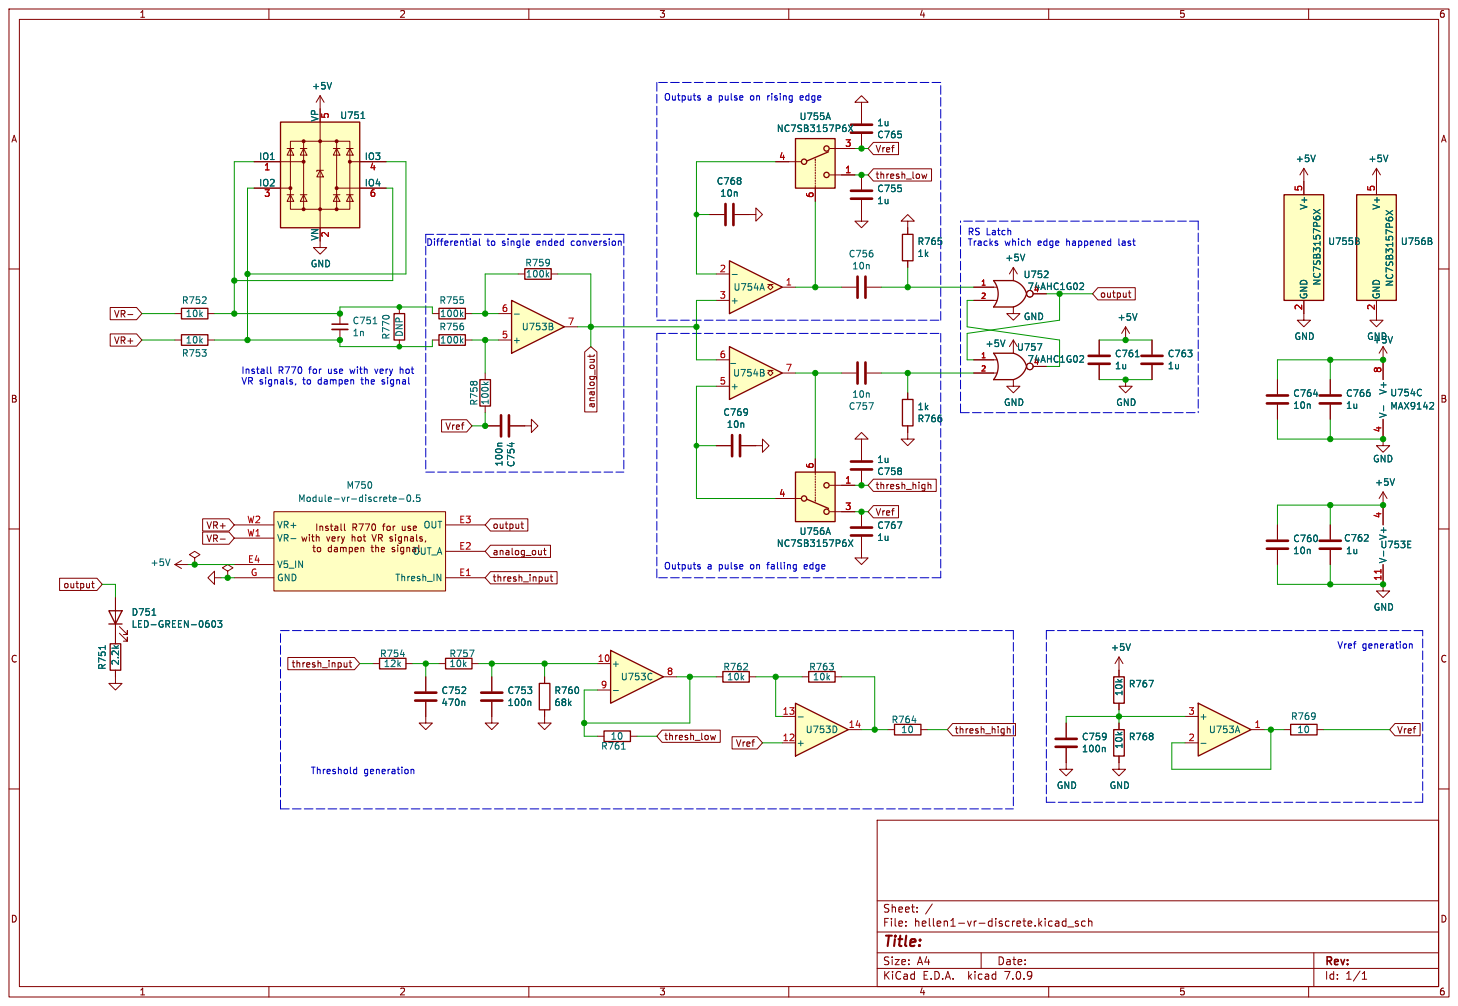
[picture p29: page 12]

Id: 1/1 Title: File: hellen1-vr-discrete.kicad_sch Sheet: /

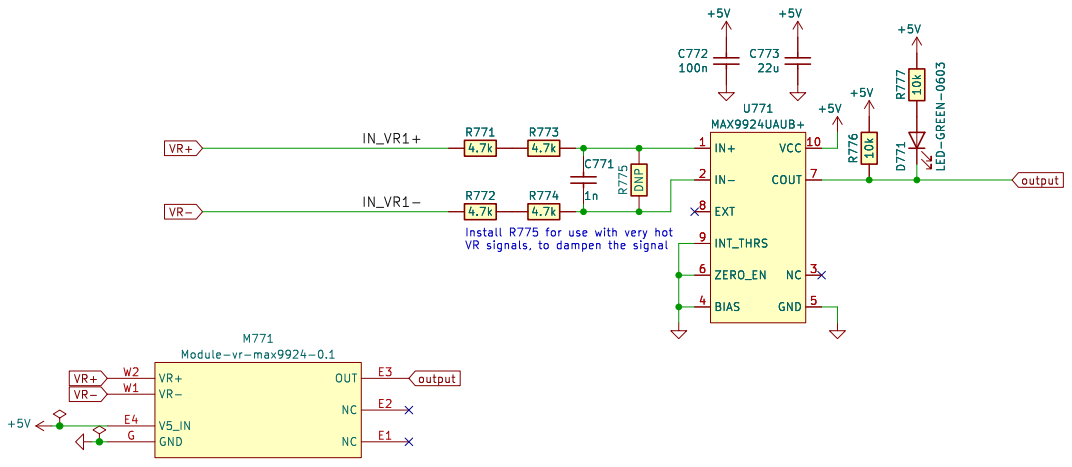
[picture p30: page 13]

File: hellen1-vr-max9924.kicad_sch Sheet: /
Id: 1/1 Title: VR MAX9924 module

+3.3V C616

27k +


100n GND GND R⁶⁰⁸ ⁴⁷

1 PA4 10 PA5 11 PA6 12 PA7 13 PB0 14 PB1 15 VSS 16 VDDIO2 17 PA8 18 PA9 19 PF0 2 PA10 20 PA11 21 PA12 22 PA13 23 PA14 24 PA15 25 PB3 26 PB4 27 PB5 28 PB6 29 PF1 3 PB7 30 PB8 31 VSSA 32 NRST 4 VDDA

1u GND GND GND
+3.3V R⁶¹¹ ²⁰k R⁶¹⁰ ²⁰k GND

to ground to improve the routing
(floating pins by the software).

Heater negative Power GND

VDDA GND
Nernst Sense Voltage Buffer Nernst Internal Resistance Measurement

+3.3V C606 DNP GND
File: hellen1-wbo.kicad_sch Sheet: / rusefi.com V⁻ 11 V⁺

Vdd 4; Vss 6; MCP6004; GNDA; OUT1; OUT2; OUT3; OUT4

Vdd 4; Vss 6; MCP6004; GNDA; OUT1; OUT2; OUT3; OUT4

SPI_; VCC; 5 SPI_SCK; 7 SPI_O; lex MicroSD; _MIS


R143 populated: analog input O2S
R145 populated: WAKEUP by CAN

*VIGN input is unprotected!
*A21 is duplicated for ADC and EINT


See pullups replacement file for actual values


# See pullups replacement file for actual values


VRE; _CRA; _CLT; IAT; _IAT; VIG; nRes; VBAT; SWCL; SPI2; _MIS; SPI3; I2C_SCL; SPI1; PWR_; GRE; u mcu.Sch; _IGN; 8.Sch; _can can.Sch; d.Sch; nRS; USB_; P USB_; USBI; A I2C_SCL UART8_RX UART8_TX UART2_RX UART2_TX; N VBAT; VCC; ACC_SC; ACC_; ACC_MIS; ACC_MO; BARO; sen; ors.Sc; LVC1; VBU; wer.Sch; USBID (PA; USBM (PA; USBP (PA; 8 SWDIO (PA13); N5 SWCLK (PA14); N6 nReset; _SCK (PC1; _MISO (PC1; _MOSI (PC1; I2C_SCL (PB1; 3 I2C_SDA (PB11); E4 UART2_TX (PD5); _SCK; _MISO (PB1; _MOSI (PB1; _PWM2 (PC6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

USBM USBP USBID VBUS
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

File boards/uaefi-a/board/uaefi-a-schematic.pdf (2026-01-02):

IGN1_(PC13) W10 | CANH | W11 CANL | W12 V33_REF W13 | V5A_SWITCHABLE W14 V5A_SWITCHABLE | W2
5569-16A2 OUT_LS_WEAK2 | OUT_IGN4


LS & HS outputs Discrete inputs

Analog/digital Heater negative Power GND

3V3 12 GND 13 EN 15 ALED 16 STAT 17 RXD 2

R5 DNP GND R³ 6.8k R² 33k

enable the CAN WAKEUP
input will be unavailable.

use ADC3 for receiving
the analog signal VR1
instead of the knock
signal

https://rusefi.com/s/h112-17
File: uaefi.kicad_sch Sheet: / rusEFI.com


D Date: 2023-11-01 KiCad; kicad-cli; 7.0.9-7.0.9~ubuntu22.04.1 Size: A4; Rev:; 2 3 Q4 ZXMS6005SGTA R10 4.7k 1; 2 3 Q1 ZXMS6005SGTA R11 4.7k K; +12V_RAW; GND; 2 3 Q3 ZXMS6005SGTA GND; +12V_RAW 1 A; D4B5819W R¹² 4.7k 1; 2 3 Q2 ZXMS6005SGTA GND; D5B5819W R¹³ 4.7k; OUT3 OUT2 OUT1; OUT4; IN3 +12V_RAW; 2 R¹³ 4.7k R¹² 4.7k; 2 Q4 ZXMS6005SGTA; 2 3 Q3 ZXMS6005SGTA; 2 3 +12V_RAW; 2 R¹¹ 4.7k R¹⁰ 4.7k Q1 ZXMS6005SGTA 1; 2 Q2 ZXMS6005SGTA

File: LS4.kicad_sch Sheet: /Low Side 2A/ rusefi.com

Id: 3/9 Title: UAEFI Low Side

D Date: 2023-11-01 KiCad; kicad-cli; 7.0.9-7.0.9~ubuntu22.04.1 Size: A4; Rev:; GND; 2 3 Q5 AO3400A GND GND; 3 D6PSM712-LF GND R16 4.7k 12; IN1 OUT1 OUT2; 2 3 GND GND; D6PSM712-LF; 3 D7PSM712-LF; 2 3 GND

3 D7PSM712-LF GND GND R15 4.7k

3 GND GND R15 4.7k R16 4.7k GND Q6 AO3400A

Id: 6/9 Title: UAEF Low Side low current File: LS_weak.kicad_sch Sheet: /Low Side/ rusefi.com

D Date: KiCad; kicad-cli; 7.0.9-7.0.9~ubuntu22.04.1 Size: A4; Rev:; VOUT; 1 GND; 2 VCC; 6 U3 MPX4/MPXH6400_MAP; GND GND; OUT U3 MPX4/MPXH6400_MAP

Id: 8/9 Title: File: MAP.kicad_sch Sheet: /MAP/


File: IGN6.kicad_sch Sheet: /Ignition/ rusefi.com

Id: 9/9 Title: UAEFI Ignition


4 SCK 5 ~{CS}6 SO 7 U4 MAX31855KASA DNP

Id: 9/9 Title: File: egt.kicad_sch Sheet: /EGT/


Id: 10/9 Title: UAEFI Injector File: INJ6.kicad_sch Sheet: /Injector/ rusefi.com

Hellen One : Power-Module interface

Reverse polarity and overvoltage protection
F410 V12_RAW


## +5VGND

## +5VGND


Outputs a pulse on rising edge R751

Vref generation RS Latch Tracks which edge happened last
4 GND GND

Differential to single ended conversion

Outputs a pulse on falling edge


Id: 1/1 Title: VR MAX9924 module

+3.3V C616

27k +


100n GND GND R⁶⁰⁸ ⁴⁷

1 PA4 10 PA5 11 PA6 12 PA7 13 PB0 14 PB1 15 VSS 16 VDDIO2 17 PA8 18 PA9 19 PF0 2 PA10 20 PA11 21 PA12 22 PA13 23 PA14 24 PA15 25 PB3 26 PB4 27 PB5 28 PB6 29 PF1 3 PB7 30 PB8 31 VSSA 32 NRST 4 VDDA

1u GND GND GND
+3.3V R⁶¹¹ ²⁰k R⁶¹⁰ ²⁰k GND

to ground to improve the routing
(floating pins by the software).

Heater negative Power GND

VDDA GND
Nernst Sense Voltage Buffer Nernst Internal Resistance Measurement

+3.3V C606 DNP GND
File: hellen1-wbo.kicad_sch Sheet: / rusefi.com V⁻ 11 V⁺

Vdd 4; Vss 6; MCP6004; GNDA; OUT1; OUT2; OUT3; OUT4; C180 PIC18001 100n; PIC18002 COC3; PIR18001; PIR18002; PIR18003; PIR18004; PIR18005; PIR18006; PIR18007; PIR18008; COR5; PIR18101; PIR18102; PIR18103; PIR18105; PIR18104; PIR18106; PIR18107; PIR18108; COR6; PIU18001; PIU18002; PIU18003; PIU18004; PIU18005; PIU18006; PIU18007; PIU18008; PIU18009; PIU180010; PIU180011; PIU180012; PIU180013; PIU180014; COU2; PIC18001; POOUT2; POOUT1; POOUT3; POOUT4; POIN1; POIN3 PIU18005; PIU180010 POIN4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

Vdd 4; Vss 6; MCP6004; GNDA; OUT1; OUT2; OUT3; OUT4; C185 PIC18501 100n; PIC18502 COC3; PIR18501; PIR18502; PIR18503; PIR18504; PIR18505; PIR18506; PIR18507; PIR18508; COR5; PIR18601; PIR18602; PIR18603; PIR18605; PIR18604; PIR18606; PIR18607; PIR18608; COR6; PIU18501; PIU18502; PIU18503; PIU18504; PIU18505; PIU18506; PIU18507; PIU18508; PIU18509; PIU185010; PIU185011; PIU185012; PIU185013; PIU185014; COU2; PIC18501; POOUT2; POOUT1; POOUT3; POOUT4; POIN1; POIN3 PIU18505; PIU185010 POIN4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

SPI_; VCC; 5 SPI_SCK; 7 SPI_O; lex MicroSD; _MIS


R143 populated: analog input O2S
R145 populated: WAKEUP by CAN

*VIGN input is unprotected!
*A21 is duplicated for ADC and EINT



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

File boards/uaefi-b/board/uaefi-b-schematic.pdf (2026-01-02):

# 3V3 DC Driver 2 OUT5

# IN3 Ignition OUT+ OUT- PWR PWM


Bus types General purpose bus

Injection Discrete inputs LS & HS outputs Analog inputs (sensors) DC Motor

Analog/digital Heater negative Power GND

3V3 12 GND 13 EN 15 ALED 16 STAT 17 RXD 2

enable the CAN WAKEUP
input will be unavailable.

use ADC3 for receiving
the analog signal VR1
instead of the knock

Hellen-One-PCB-logo

https://rusefi.com/s/uaefi
Id: 1/9 Title: UAEFI File: uaefi.kicad_sch Sheet: / rusEFI.com


D Date: 2023-11-01 KiCad; kicad-cli; 7.0.10-7.0.10~ubuntu22.04.1 Size: A4; Rev:; GND; +12V_RAW; GND GND; GND R¹² 4.7k; R¹¹ 4.7k +12V_RAW; R¹³ 4.7k GND; 1 STATUS1; 3 STATUS2; U8 VNLD5160TR-E; U7 VNLD5160TR-E; R¹⁰ 4.7k; OUT1 OUT4 OUT3; IN1 OUT2; R¹⁰ 4.7k GND GND R¹³ 4.7k GND R¹¹ 4.7k; R¹² 4.7k GND

File: LS4.kicad_sch Sheet: /LS/ rusefi.com

Id: 3/9 Title: UAEFI Low Side

D Date: 2023-11-01 KiCad; kicad-cli; 7.0.10-7.0.10~ubuntu22.04.1 Size: A4; Rev:; Id: 6/9 Title: UAEF Low Side always hot File: LS_HOT.kicad_sch Sheet: /LS; HOT/ rusefi.com; GND R¹⁶ 4.7k GND; R¹⁵ 4.7k; 1 STATUS1; 3 STATUS2; U6 VNLD5160TR-E GND; IN2 OUT1 OUT2; R¹⁵ 4.7k GND R¹⁶ 4.7k; GND

D Date: KiCad; kicad-cli; 7.0.10-7.0.10~ubuntu22.04.1 Size: A4; Rev:; VOUT; 1 GND; 2 VCC; 6 U3 MPX4/MPXH6400_MAP; GND GND; OUT U3 MPX4/MPXH6400_MAP

Id: 8/9 Title: File: MAP.kicad_sch Sheet: /MAP/


File: IGN6.kicad_sch Sheet: /Ignition/ rusefi.com

Id: 9/9 Title: UAEFI Ignition


4 SCK 5 ~{CS}6 SO 7 U4 MAX31855KASA DNP

Id: 9/9 Title: File: egt.kicad_sch Sheet: /EGT/

6 ABCD; ABCD Date: 2023-11-01 KiCad; kicad-cli; 7.0.10-7.0.10~ubuntu22.04.1 Size: A4; Rev:; Id: 10/9 Title: UAEFI Injector File: INJ6.kicad_sch Sheet: /Injector/ rusefi.comR³³ 4.7k GND R³⁴ 4.7k GND GND R³² 4.7k; GND R³¹ 4.7k R³⁰ 4.7k GND; R²⁹ 4.7k GND; 1 STATUS1; 3 STATUS2; U9 VNLD5160TR-E GND GND; U11 VNLD5160TR-E GND; U10 VNLD5160TR-E OUT6; IN5 OUT4 OUT3 OUT5 OUT2 OUT1; GND R³⁰ 4.7k; R³¹ 4.7k GND R³² 4.7k GND GND R³⁴ 4.7k; GND R²⁹ 4.7k GND R³³ 4.7k

Hellen One : Power-Module interface

Reverse polarity and overvoltage protection
F410 V12_RAW


## +5VGND

## +5VGND


Outputs a pulse on rising edge R751

Vref generation RS Latch Tracks which edge happened last
4 GND GND

Differential to single ended conversion

Outputs a pulse on falling edge


Id: 1/1 Title: VR MAX9924 module

+3.3V C616

27k +


100n GND GND R⁶⁰⁸ ⁴⁷

1 PA4 10 PA5 11 PA6 12 PA7 13 PB0 14 PB1 15 VSS 16 VDDIO2 17 PA8 18 PA9 19 PF0 2 PA10 20 PA11 21 PA12 22 PA13 23 PA14 24 PA15 25 PB3 26 PB4 27 PB5 28 PB6 29 PF1 3 PB7 30 PB8 31 VSSA 32 NRST 4 VDDA

1u GND GND GND
+3.3V R⁶¹¹ ²⁰k R⁶¹⁰ ²⁰k GND

to ground to improve the routing
(floating pins by the software).

Heater negative Power GND

VDDA GND
Nernst Sense Voltage Buffer Nernst Internal Resistance Measurement

+3.3V C606 DNP GND
File: hellen1-wbo.kicad_sch Sheet: / rusefi.com V⁻ 11 V⁺

Vdd 4; Vss 6; MCP6004; GNDA; OUT1; OUT2; OUT3; OUT4; C180 PIC18001 100n; PIC18002 COC3; PIR18001; PIR18002; PIR18003; PIR18004; PIR18005; PIR18006; PIR18007; PIR18008; COR5; PIR18101; PIR18102; PIR18103; PIR18105; PIR18104; PIR18106; PIR18107; PIR18108; COR6; PIU18001; PIU18002; PIU18003; PIU18004; PIU18005; PIU18006; PIU18007; PIU18008; PIU18009; PIU180010; PIU180011; PIU180012; PIU180013; PIU180014; COU2; PIC18001; POOUT2; POOUT1; POOUT3; POOUT4; POIN1; POIN3 PIU18005; PIU180010 POIN4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

Vdd 4; Vss 6; MCP6004; GNDA; OUT1; OUT2; OUT3; OUT4; C185 PIC18501 100n; PIC18502 COC3; PIR18501; PIR18502; PIR18503; PIR18504; PIR18505; PIR18506; PIR18507; PIR18508; COR5; PIR18601; PIR18602; PIR18603; PIR18605; PIR18604; PIR18606; PIR18607; PIR18608; COR6; PIU18501; PIU18502; PIU18503; PIU18504; PIU18505; PIU18506; PIU18507; PIU18508; PIU18509; PIU185010; PIU185011; PIU185012; PIU185013; PIU185014; COU2; PIC18501; POOUT2; POOUT1; POOUT3; POOUT4; POIN1; POIN3 PIU18505; PIU185010 POIN4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

SPI_; VCC; 5 SPI_SCK; 7 SPI_O; lex MicroSD; _MIS


R143 populated: analog input O2S
R145 populated: WAKEUP by CAN

*VIGN input is unprotected!
*A21 is duplicated for ADC and EINT



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

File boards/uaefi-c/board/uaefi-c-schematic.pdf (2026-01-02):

IN2 OUT1 | IN1 OUT2 LS HOT OUT+ OUT- PWR | PWM

# IN3 LS OUT5


Analog/digital Heater negative Power GND

3V3 12 GND 13 EN 15 ALED 16 STAT 17 RXD 2

enable the CAN WAKEUP
input will be unavailable.

analog signal VR-DISCRETE
instead of the knock signal

Hellen-One-PCB-logo

https://rusefi.com/s/uaefi
Id: 1/9 Title: UAEFI File: uaefi.kicad_sch Sheet: / rusEFI.com


D Date: 2023-11-01 KiCad; kicad-cli; 7.0.11-7.0.11~ubuntu22.04.1 Size: A4; Rev:; GND; +12V_RAW; GND GND; GND R¹² 4.7k; R¹¹ 4.7k +12V_RAW; R¹³ 4.7k GND; 1 STATUS1; 3 STATUS2; U8 VNLD5160TR-E; U7 VNLD5160TR-E; R¹⁰ 4.7k; OUT1 OUT4 OUT3; IN1 OUT2; R¹⁰ 4.7k GND GND R¹³ 4.7k GND R¹¹ 4.7k; R¹² 4.7k GND

File: LS4.kicad_sch Sheet: /LS/ rusefi.com

Id: 3/9 Title: UAEFI Low Side

D Date: 2023-11-01 KiCad; kicad-cli; 7.0.11-7.0.11~ubuntu22.04.1 Size: A4; Rev:; Id: 6/9 Title: UAEF Low Side always hot File: LS_HOT.kicad_sch Sheet: /LS; HOT/ rusefi.com; GND R¹⁶ 4.7k GND; R¹⁵ 4.7k; 1 STATUS1; 3 STATUS2; U6 VNLD5160TR-E GND; IN2 OUT1 OUT2; R¹⁵ 4.7k GND R¹⁶ 4.7k; GND

D Date: KiCad; kicad-cli; 7.0.11-7.0.11~ubuntu22.04.1 Size: A4; Rev:; VOUT; 1 GND; 2 VCC; 6 U3 MPX4/MPXH6400_MAP; GND GND; OUT U3 MPX4/MPXH6400_MAP

Id: 8/9 Title: File: MAP.kicad_sch Sheet: /MAP/


File: IGN6.kicad_sch Sheet: /Ignition/ rusefi.com

Id: 9/9 Title: UAEFI Ignition


Id: 9/9 Title: File: egt.kicad_sch Sheet: /EGT/

6 ABCD; ABCD Date: 2023-11-01 KiCad; kicad-cli; 7.0.11-7.0.11~ubuntu22.04.1 Size: A4; Rev:; Id: 10/9 Title: UAEFI Injector File: INJ6.kicad_sch Sheet: /Injector/ rusefi.comR³³ 4.7k GND R³⁴ 4.7k GND GND R³² 4.7k; GND R³¹ 4.7k R³⁰ 4.7k GND; R²⁹ 4.7k GND; 1 STATUS1; 3 STATUS2; U9 VNLD5160TR-E GND GND; U11 VNLD5160TR-E GND; U10 VNLD5160TR-E OUT6; IN5 OUT4 OUT3 OUT5 OUT2 OUT1; GND R³⁰ 4.7k; R³¹ 4.7k GND R³² 4.7k GND GND R³⁴ 4.7k; GND R²⁹ 4.7k GND R³³ 4.7k

Hellen One : Power-Module interface

Reverse polarity and overvoltage protection
F410 V12_RAW


# 6 U751 GND

1u R761


Id: 1/1 Title: File: hellen1-vr-discrete.kicad_sch Sheet: /


File: hellen1-vr-max9924.kicad_sch Sheet: /
Id: 1/1 Title: VR MAX9924 module

+3.3V C616

27k +


100n GND GND R⁶⁰⁸ ⁴⁷

1 PA4 10 PA5 11 PA6 12 PA7 13 PB0 14 PB1 15 VSS 16 VDDIO2 17 PA8 18 PA9 19 PF0 2 PA10 20 PA11 21 PA12 22 PA13 23 PA14 24 PA15 25 PB3 26 PB4 27 PB5 28 PB6 29 PF1 3 PB7 30 PB8 31 VSSA 32 NRST 4 VDDA

1u GND GND GND
+3.3V R⁶¹¹ ²⁰k R⁶¹⁰ ²⁰k GND

to ground to improve the routing
(floating pins by the software).

Heater negative Power GND

VDDA GND
Nernst Sense Voltage Buffer Nernst Internal Resistance Measurement

+3.3V C606 DNP GND
File: hellen1-wbo.kicad_sch Sheet: / rusefi.com V⁻ 11 V⁺

Vdd 4; Vss 6; MCP6004; GNDA; OUT1; OUT2; OUT3; OUT4; C180 PIC18001 100n; PIC18002 COC3; PIR18001; PIR18002; PIR18003; PIR18004; PIR18005; PIR18006; PIR18007; PIR18008; COR5; PIR18101; PIR18102; PIR18103; PIR18105; PIR18104; PIR18106; PIR18107; PIR18108; COR6; PIU18001; PIU18002; PIU18003; PIU18004; PIU18005; PIU18006; PIU18007; PIU18008; PIU18009; PIU180010; PIU180011; PIU180012; PIU180013; PIU180014; COU2; PIC18001; POOUT2; POOUT1; POOUT3; POOUT4; POIN1; POIN3 PIU18005; PIU180010 POIN4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

Vdd 4; Vss 6; MCP6004; GNDA; OUT1; OUT2; OUT3; OUT4; C185 PIC18501 100n; PIC18502 COC3; PIR18501; PIR18502; PIR18503; PIR18504; PIR18505; PIR18506; PIR18507; PIR18508; COR5; PIR18601; PIR18602; PIR18603; PIR18605; PIR18604; PIR18606; PIR18607; PIR18608; COR6; PIU18501; PIU18502; PIU18503; PIU18504; PIU18505; PIU18506; PIU18507; PIU18508; PIU18509; PIU185010; PIU185011; PIU185012; PIU185013; PIU185014; COU2; PIC18501; POOUT2; POOUT1; POOUT3; POOUT4; POIN1; POIN3 PIU18505; PIU185010 POIN4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

SPI_; VCC; 5 SPI_SCK; 7 SPI_O; lex MicroSD; _MIS


R143 populated: analog input O2S
R145 populated: WAKEUP by CAN

*VIGN input is unprotected!
*A21 is duplicated for ADC and EINT



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

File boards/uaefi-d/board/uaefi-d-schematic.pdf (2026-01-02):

IN3 Ignition OUT+ OUT- PWR | PWM
IGN1_(PC13) W10 | CANH | W11 CANL | W12 V33_REF W13 | V5A_SWITCHABLE W14 V5A_SWITCHABLE | W2


LS & HS outputs Discrete inputs

Analog/digital Heater negative Power GND

3V3 12 GND 13 EN 15 ALED 16 STAT 17 RXD 2

enable the CAN WAKEUP

analog signal VR-DISCRETE
instead of the knock signal

https://rusefi.com/s/uaefi
Id: 1/9 Title: UAEFI File: uaefi.kicad_sch Sheet: / rusEFI.com


D Date: 2024-08-15 KiCad; E.D.A. 8.0.4 Size: A4; Rev:; GND; +12V_RAW; GND GND; GND R¹² 4.7k; R¹¹ 4.7k +12V_RAW; R¹³ 4.7k GND; 1 STATUS1; 3 STATUS2; U8 VNLD5160TR-E; U7 VNLD5160TR-E; R¹⁰ 4.7k; OUT1 OUT4 OUT3; IN1 OUT2; R¹⁰ 4.7k GND GND R¹³ 4.7k GND R¹¹ 4.7k; R¹² 4.7k GND

Id: 3/9 Title: UAEFI File: LS4.kicad_sch Sheet: /LS/ rusEFI.com

D Date: 2024-08-15 KiCad; E.D.A. 8.0.4 Size: A4; Rev:; Id: 6/9 Title: UAEFI File: LS_HOT.kicad_sch Sheet: /LS; HOT/ rusEFI.com; GND R¹⁶ 4.7k GND; R¹⁵ 4.7k; 1 STATUS1; 3 STATUS2; U6 VNLD5160TR-E GND; IN2 OUT1 OUT2; R¹⁵ 4.7k GND R¹⁶ 4.7k; GND

D Date: 2024-08-15 KiCad; E.D.A. 8.0.4 Size: A4; Rev:; VOUT; 1 GND; 2 VCC; 6 U3 MPX4/MPXH6400_MAP; GND GND; OUT U3 MPX4/MPXH6400_MAP

Id: 8/9 Title: UAEFI File: MAP.kicad_sch Sheet: /MAP/ rusEFI.com


Id: 9/9 Title: UAEFI File: IGN6.kicad_sch Sheet: /Ignition/ rusEFI.com


Id: 9/9 Title: UAEFI File: egt.kicad_sch Sheet: /EGT/ rusEFI.com GND

6 ABCD; ABCD Date: 2024-08-15 KiCad; E.D.A. 8.0.4 Size: A4; Rev:; Id: 10/9 Title: UAEFI File: INJ6.kicad_sch Sheet: /Injector/ rusEFI.comR³³ 4.7k GND R³⁴ 4.7k GND GND R³² 4.7k; GND R³¹ 4.7k R³⁰ 4.7k GND; R²⁹ 4.7k GND; 1 STATUS1; 3 STATUS2; U9 VNLD5160TR-E GND GND; U11 VNLD5160TR-E GND; U10 VNLD5160TR-E OUT6; IN5 OUT4 OUT3 OUT5 OUT2 OUT1; GND R³⁰ 4.7k; R³¹ 4.7k GND R³² 4.7k GND GND R³⁴ 4.7k; GND R²⁹ 4.7k GND R³³ 4.7k

Hellen One : Power-Module interface

Reverse polarity and overvoltage protection
F410 V12_RAW


# 6 U751 GND

1u R761


Id: 1/1 Title: File: hellen1-vr-discrete.kicad_sch Sheet: /


File: hellen1-vr-max9924.kicad_sch Sheet: /
Id: 1/1 Title: VR MAX9924 module

+3.3V C616

27k +


100n GND GND R⁶⁰⁸ ⁴⁷

1 PA4 10 PA5 11 PA6 12 PA7 13 PB0 14 PB1 15 VSS 16 VDDIO2 17 PA8 18 PA9 19 PF0 2 PA10 20 PA11 21 PA12 22 PA13 23 PA14 24 PA15 25 PB3 26 PB4 27 PB5 28 PB6 29 PF1 3 PB7 30 PB8 31 VSSA 32 NRST 4 VDDA

1u GND GND GND
+3.3V R⁶¹¹ ²⁰k R⁶¹⁰ ²⁰k GND

to ground to improve the routing
(floating pins by the software).

Heater negative Power GND

VDDA GND
Nernst Sense Voltage Buffer Nernst Internal Resistance Measurement

+3.3V C606 DNP GND
File: hellen1-wbo.kicad_sch Sheet: / rusefi.com V⁻ 11 V⁺

Vdd 4; Vss 6; MCP6004; GNDA; OUT1; OUT2; OUT3; OUT4; C180 PIC18001 100n; PIC18002 COC3; PIR18001; PIR18002; PIR18003; PIR18004; PIR18005; PIR18006; PIR18007; PIR18008; COR5; PIR18101; PIR18102; PIR18103; PIR18105; PIR18104; PIR18106; PIR18107; PIR18108; COR6; PIU18001; PIU18002; PIU18003; PIU18004; PIU18005; PIU18006; PIU18007; PIU18008; PIU18009; PIU180010; PIU180011; PIU180012; PIU180013; PIU180014; COU2; PIC18001; POOUT2; POOUT1; POOUT3; POOUT4; POIN1; POIN3 PIU18005; PIU180010 POIN4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

Vdd 4; Vss 6; MCP6004; GNDA; OUT1; OUT2; OUT3; OUT4; C185 PIC18501 100n; PIC18502 COC3; PIR18501; PIR18502; PIR18503; PIR18504; PIR18505; PIR18506; PIR18507; PIR18508; COR5; PIR18601; PIR18602; PIR18603; PIR18605; PIR18604; PIR18606; PIR18607; PIR18608; COR6; PIU18501; PIU18502; PIU18503; PIU18504; PIU18505; PIU18506; PIU18507; PIU18508; PIU18509; PIU185010; PIU185011; PIU185012; PIU185013; PIU185014; COU2; PIC18501; POOUT2; POOUT1; POOUT3; POOUT4; POIN1; POIN3 PIU18505; PIU185010 POIN4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

SPI_; VCC; 5 SPI_SCK; 7 SPI_O; lex MicroSD; _MIS


R143 populated: analog input O2S
R145 populated: WAKEUP by CAN

*VIGN input is unprotected!
*A21 is duplicated for ADC and EINT



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

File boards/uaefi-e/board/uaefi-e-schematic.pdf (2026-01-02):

3V3 | DC Driver 1 OUT5
IGN1_(PC13) W10 | CANH | W11 CANL | W12 V33_REF W13 | V5A_SWITCHABLE W14 V5A_SWITCHABLE | W2


Injection General purpose bus

Analog inputs (sensors) LS & HS outputs Discrete inputs A
8 +12V_RAW

Analog/digital Heater negative Power GND

3V3 12 GND 13 EN 15 ALED 16 STAT 17 RXD 2

enable the CAN WAKEUP

analog signal VR-DISCRETE

https://rusefi.com/s/uaefi
Id: 1/9 Title: UAEFI File: uaefi.kicad_sch Sheet: / rusEFI.com


D Date: 2025-04-30 KiCad; E.D.A. 8.0.9 Size: A4; Rev:; GND GND; GND R¹² 4.7k R¹¹ 4.7k GND GND; R¹³ 4.7k; 1 STATUS1; 3 STATUS2; U7 VNLD5160TR-E; U8 VNLD5160TR-E; R¹⁰ 4.7k GND; IN2 OUT1; IN4 OUT3 OUT2 OUT4; R¹⁰ 4.7k GND GND R¹³ 4.7k GND R¹¹ 4.7k; R¹² 4.7k GND

Id: 3/9 Title: UAEFI File: LS4.kicad_sch Sheet: /LS/ rusEFI.com
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

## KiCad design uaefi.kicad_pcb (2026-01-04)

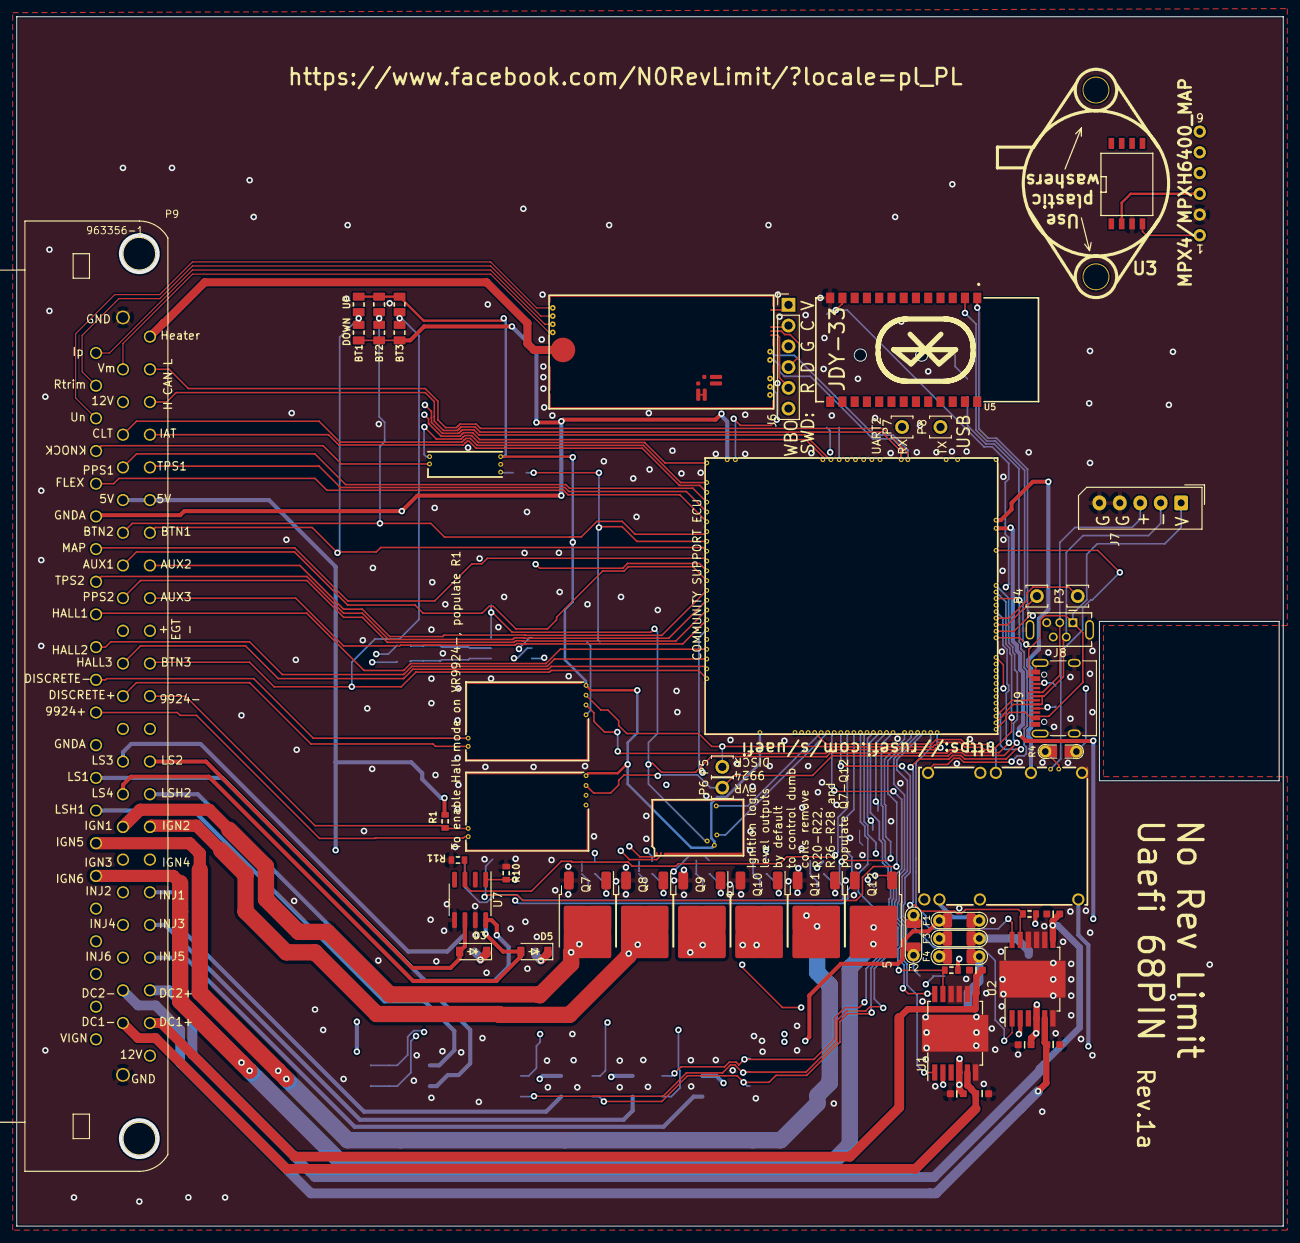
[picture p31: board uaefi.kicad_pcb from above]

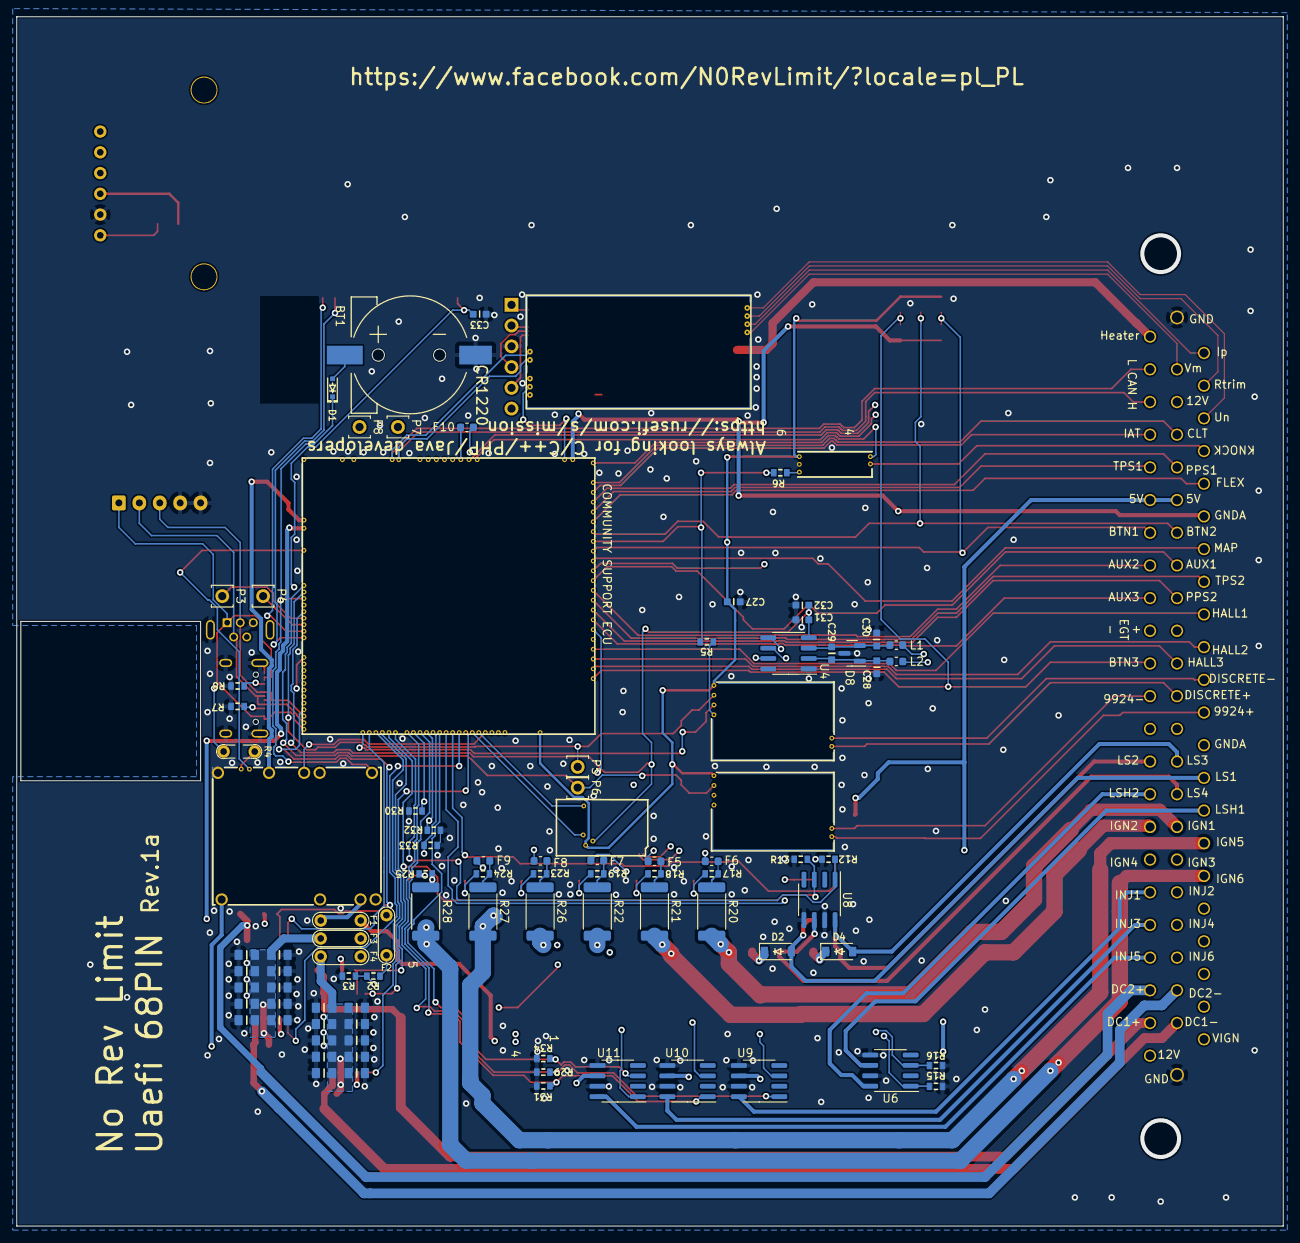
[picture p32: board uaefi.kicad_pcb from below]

Board: 4 copper layers, 155.0 x 148.0 mm, 127 parts (74 on the bottom side), 140 nets.

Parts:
BT1: CR1220; CR1220-2
C1, C2, C3, C4, C5, C6, C7, C8, C9, C10, C14, C15, C16, C17, C18, C19, C20, C21, C22, C23: 10u; C0805
C11, C24, C27, C29, C31, C33: 100n; C0603
C12, C13, C25, C26, C28, C30: 10n; C0603
C32: 1u; C0603
D1: 1N4148WS; SOD-323
D2, D3, D4, D5: B5819W; SOD-123
D8: NUP2105L; SOT-23
F1, F2, F3, F4: 12H1500D; PAD-1206-PAD
F5, F6, F7, F8, F9, F10: 50mA; Fuse_0603_1608Metric
J6: Conn_01x06; PinHeader_1x06_P2.54mm_Vertical
J7: Conn_01x05_Male; Molex_SPOX_5267-05A_1x05_P2.50mm_Vertical
J8: USB_B_Mini; USB-MINI-B-VERTICAL
J9: USB_C
L1, L2: 470R@100MHz; L_0603_1608Metric
M1: Module-power_12and5V-0.3; power_12and5V
M2: Module-knock-0.2; knock
M3: Module-vr-discrete-0.5; vr-discrete
M4: Module-vr-max9924-0.1; vr-max9924
M5: Module-wbo-0.5; wbo
M6: Module:mega-mcu100/0.3; mega-mcu100
M7: Module-can-0.1; can
P3, P4, P5, P6, P7, P8: Pad; PAD-TH
P9: 963356-1
Q7, Q8, Q9, Q10, Q11, Q12: ISL9V3040D3ST; TO-252-2
R1, R9, R10, R11, R12, R13, R14, R15, R16, R29, R30, R31, R32, R33, R34: 4.7k; R0603
R2: 33k; R0603
R3: 6.8k; R0603
R4: Jumper-Pad-Pad; PAD-0805-PAD
R5, R6: 0; R0603
R7, R8: 5.6k; R0603
R17, R18, R19, R23, R24, R25: 22; R0603
R20, R21, R22, R26, R27, R28: 0; R_2512_6332Metric
R35, R36, R37: 10k; R0805
R38, R39, R40: DNP; R0805
U1, U2: TLE9201SG; Infineon_PG-DSO-12-11
U3: MPX4/MPXH6400_MAP; MPX-4_MAP
U4: MAX31855KASA; SOIC-8_3.9x4.9mm_P1.27mm
U5: JDY-33
U6, U7, U8, U9, U10, U11: VNLD5160TR-E; SOIC-8_3.9x4.9mm_P1.27mm

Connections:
+3.3V: M6.N21 (V33), R9.2, R14.2, U1.2 (VSO), U2.2 (VSO)
+3.3VA: C31.2, C32.2, C33.2, M6.N15 (V33_SWITCHABLE), M7.V2 (CAN_VIO), U4.4 (V_CC), U5.12 (3V3)
+5V: M1.E4 (V5), M6.N22 (VCC)
+5VA: C27.2, M2.E1 (V5A), M3.E4 (V5_IN), M4.E4 (V5_IN), M5.W1 (V5_IN), M6.E1 (V5A_SWITCHABLE), M6.W2 (V5A_SWITCHABLE), M7.V1 (V5), R38.2, R39.2, R40.2, U3.3 (VCC)
+5VP: M1.V4 (5VP), P9.6, P9.51, R1.1
+12V: F2.1, F3.1, F4.1, P9.68, R2.2
+12V_RAW: D2.1 (K), D3.1 (K), D4.1 (K), D5.1 (K), F2.2, M1.V1 (V12_PERM), M1.V3 (V12_RAW), P9.3
/1_WBO_Ip: M5.E3 (LSU_Ip), P9.24
/2_WBO_Vm: M5.E2 (LSU_Vm), P9.2
/3_WBO_Heater: M5.E5 (LSU_H+), P9.46
/5_WBO_Rtrim: M5.E4 (LSU_Rtrim), P9.25
/6_WBO_Un: M5.E1 (LSU_Un), P9.26
/12V_KEY: F1.1, P9.45
/ADC3: M6.S15 (IN_KNOCK_(PA2)), R5.2, R6.2
/CAN2+: M7.S2 (CANH), P9.58
/CAN2-: M7.S1 (CANL), P9.13
/CAN+: M5.W4 (CANH), M6.W11 (CANH), P9.48
/CAN-: M5.W3 (CANL), M6.W12 (CANL), P9.47
/DC1_DIR: M6.E21 (OUT_PWM4_(PC8)), U1.1 (DIR)
/DC1_DIS: M6.E8 (SPI2_MISO_(PB14)), R9.1, U1.11 (DIS)
/DC1_PWM: M6.E20 (OUT_PWM3_(PC7)), U1.12 (PWM)
/DC2_DIR: M6.E9 (SPI2_MOSI_(PB15)), U2.1 (DIR)
/DC2_DIS: M6.N4 (USBID_(PA10)), R14.1, U2.11 (DIS)
/DC2_PWM: M6.E22 (OUT_PWM5_(PC9)), U2.12 (PWM)
/DC Driver 1/PWR: C1.2, C2.2, C3.2, C4.2, C5.2, C6.2, C7.2, C8.2, C9.2, C10.2, C11.2, F4.2, U1.4 (VS)
/DC Driver 2/PWR: C14.2, C15.2, C16.2, C17.2, C18.2, C19.2, C20.2, C21.2, C22.2, C23.2, C24.2, F3.2, U2.4 (VS)
/EGT+: L1.1, P9.10
/EGT-: L2.1, P9.55
/EGT/SPI_CS: M6.N9 (SPI3_CS_(PA15)), U4.6 (~CS)
/IGN1: F6.2, M6.W10 (IGN1_(PC13))
/IGN2: F5.2, M6.W9 (IGN2_(PE5))
/IGN3: F7.2, M6.W8 (IGN3_(PE4))
/IGN4: F8.2, M6.W7 (IGN4_(PE3))
/IGN5: F9.2, M6.W6 (IGN5_(PE2))
/IGN6: F10.2, M6.W5 (IGN6_(PB8))
/INJ1: M6.E17 (OUT_INJ1_(PD3)), R29.2, U9.1 (IN1)
/INJ2: M6.E16 (OUT_INJ2_(PA9)), R30.2, U9.3 (IN2)
/INJ3: M6.E15 (OUT_INJ3_(PD11)), R31.2, U10.1 (IN1)
/INJ4: M6.E14 (OUT_INJ4_(PD10)), R32.2, U10.3 (IN2)
/INJ5: M6.E13 (OUT_INJ5_(PD2)), R33.2, U11.1 (IN1)
/INJ6: M6.E12 (OUT_INJ6_(PA8)), R34.2, U11.3 (IN2)
/INTERNAL_MAP: M6.S12 (IN_MAP2_(PC1)), U3.1 (VOUT)
/IN_AUX1: M6.S11 (IN_O2S_/_CAN_WAKEUP_(PA0)), P9.8
/IN_AUX2: M6.S10 (IN_O2S2_(PA1)), P9.53
/IN_AUX3: M6.S7 (IN_AUX3_(PA7)), P9.54
/IN_BUTTON1: M6.S14 (IN_CRANK_(PB1)), P9.52, R35.2, R38.1
/IN_BUTTON2: M6.S16 (IN_CAM_(PA6)), P9.7, R36.2, R39.1
/IN_BUTTON3: M6.S1 (IN_D4_(PE15)), P9.56, R37.2, R40.1
/IN_CLT: M6.S21 (IN_CLT_(PC2)), P9.4
/IN_FLEX: M6.S17 (IN_VSS_(PE11)), P9.28
/IN_HALL1: M6.S4 (IN_D1_(PE12)), P9.32
/IN_HALL2: M6.S3 (IN_D2_(PE13)), P9.33
/IN_HALL3: M6.S2 (IN_D3_(PE14)), P9.11
/IN_IAT: M6.S20 (IN_IAT_(PC3)), P9.49
/IN_KNOCK: M2.E3 (OUT_KNOCK), R6.1
/IN_KNOCK_RAW: M2.W1 (IN_KNOCK), P9.27
/IN_MAP: M6.S13 (IN_MAP1_(PC0)), P9.30
/IN_PPS1: M6.S19 (IN_PPS_(PA3)), P9.5
/IN_PPS2: M6.S8 (IN_AUX2_(PC4/PE9)), P9.9
/IN_TPS1: M6.S18 (IN_TPS_(PA4)), P9.50
/IN_TPS2: M6.S9 (IN_AUX1_(PB0)), P9.31
/IN_VIGN: F1.2, M1.V2 (IN_VIGN)
/IN_VMAIN: M6.S6 (IN_AUX4_(PC5)), R2.1, R3.2
/LS1: M6.E11 (OUT_INJ7_(PD15)), R10.2, U7.1 (IN1)
/LS2: M6.E10 (OUT_INJ8_(PD12)), R11.2, U7.3 (IN2)
/LS3: M6.E18 (OUT_PWM1_(PD13)), R12.2, U8.1 (IN1)
/LS4: M6.E19 (OUT_PWM2_(PC6)), R13.2, U8.3 (IN2)
/LS_HOT1: M6.W4 (IGN7_(PB9)), R16.1, U6.3 (IN2)
/LS_HOT2: M6.W3 (IGN8_(PE6)), R15.1, U6.1 (IN1)
/MISO3: M6.N11 (SPI3_MISO_(PC11)), U4.7 (SO)
/OUT_DC1+: C13.2, P9.67, U1.7 (OUT2)
/OUT_DC1-: C12.2, P9.22, U1.5 (OUT1)
/OUT_DC2+: C26.2, P9.66, U2.7 (OUT2)
/OUT_DC2-: C25.2, P9.21, U2.5 (OUT1)
/OUT_IGN1: P9.16, Q7.2 (C), R20.2
/OUT_IGN2: P9.61, Q8.2 (C), R21.2
/OUT_IGN3: P9.17, Q9.2 (C), R22.2
/OUT_IGN4: P9.62, Q10.2 (C), R26.2
/OUT_IGN5: P9.39, Q11.2 (C), R27.2
/OUT_IGN6: P9.40, Q12.2 (C), R28.2
/OUT_INJ1: P9.63, U9.8 (D1)
/OUT_INJ2: P9.18, U9.6 (D2)
/OUT_INJ3: P9.64, U10.8 (D1)
/OUT_INJ4: P9.19, U10.6 (D2)
/OUT_INJ5: P9.65, U11.8 (D1)
/OUT_INJ6: P9.20, U11.6 (D2)
/OUT_LS1: D2.2 (A), P9.37, U7.8 (D1)
/OUT_LS2: D3.2 (A), P9.59, U7.6 (D2)
/OUT_LS3: D4.2 (A), P9.14, U8.8 (D1)
/OUT_LS4: D5.2 (A), P9.15, U8.6 (D2)
/OUT_LS_HOT1: P9.38, U6.6 (D2)
/OUT_LS_HOT2: P9.60, U6.8 (D1)
/PG_5VP: M6.N12 (SPI3_MOSI_(PC12)), R4.2
/PWR_EN: M1.E5 (EN_5VP), M6.N20 (OUT_PWR_EN_(PE10))
/SCK3: M6.N10 (SPI3_SCK_(PC10)), U4.5 (SCK)
/USB+: J7.3, J8.3 (D+), J9.A6 (D+), J9.B6 (D+), M6.N3 (USBP_(PA12))
/USB-: J7.2, J8.2 (D-), J9.A7 (D-), J9.B7 (D-), M6.N2 (USBM_(PA11))
/VBAT: D1.1 (K), M1.E1 (VBAT), M6.N17 (VBAT)
/VBUS: J7.1, J8.1 (VBUS), J9.A4 (VBUS), J9.A9 (VBUS), J9.B4 (VBUS), J9.B9 (VBUS), M6.N1 (VBUS)
/VIGN: M1.E3 (VIGN), M6.E5 (IN_VIGN_(PA5))
/VREF1: M2.W2 (VREF), M6.S22 (VREF1)
/VR_DISCRETE: M3.E3 (OUT), M6.N18 (UART8_RX_(PE0)), P5.1
/VR_DISCRETE+: M3.W2 (VR+), P9.12
/VR_DISCRETE-: M3.W1 (VR-), P9.34
/VR_DISCRETE_A: M3.E2 (OUT_A), R5.1
/VR_DISCRETE_THR: M3.E1 (Thresh_IN), M6.E23 (OUT_PWM6_(PD14))
/VR_MAX9924: M4.E3 (OUT), M6.N19 (UART8_TX_(PE1)), P6.1
/VR_MAX9924+: M4.W2 (VR+), P9.35
/VR_MAX9924-: M4.W1 (VR-), P9.57, R1.2
GND: BT1.2 (-), C1.1, C2.1, C3.1, C4.1, C5.1, C6.1, C7.1, C8.1, C9.1, C10.1, C11.1, C12.1, C13.1, C14.1, C15.1, C16.1, C17.1, C18.1, C19.1, C20.1, C21.1, C22.1, C23.1, C24.1, C25.1, C26.1, C27.1, C28.1, C30.1, C31.1, C32.1, C33.1, D8.3 (A), J6.3, J7.4, J7.5, J8.5 (GND), J8.6 (Shield), J9.A1 (GND), J9.A12 (GND), J9.B1 (GND), J9.B12 (GND), J9.S1 (SHIELD), M1.S1 (GND), M2.E2 (GND), M3.G (GND), M4.G (GND), M5.E6 (LSU_H-), M5.G (GND), M6.G (GND), M7.E1 (GND), P9.1, P9.23, Q7.3 (E), Q8.3 (E), Q9.3 (E), Q10.3 (E), Q11.3 (E), Q12.3 (E), R3.1, R7.1, R8.1, R10.1, R11.1, R12.1, R13.1, R15.2, R16.2, R29.1, R30.1, R31.1, R32.1, R33.1, R34.1, U1.6 (GND), U1.8 (SI), U1.9 (CSN), U1.10 (SCK), U1.13 (GND), U2.6 (GND), U2.8 (SI), U2.9 (CSN), U2.10 (SCK), U2.13 (GND), U3.2 (GND), U4.1 (GND), U5.13 (GND), U6.5 (S2), U6.7 (S1), U7.5 (S2), U7.7 (S1), U8.5 (S2), U8.7 (S1), U9.5 (S2), U9.7 (S1), U10.5 (S2), U10.7 (S1), U11.5 (S2), U11.7 (S1)
GNDA: M6.W1 (GNDA), P9.29, P9.36, R35.1, R36.1, R37.1
unnamed: BT1.1 (+), D1.2 (A)
unnamed: F5.1, R18.2, R21.1
unnamed: F6.1, R17.2, R20.1
unnamed: F7.1, R19.2, R22.1
unnamed: F8.1, R23.2, R26.1
unnamed: F9.1, R24.2, R27.1
unnamed: F10.1, R25.2, R28.1
unnamed: J6.1, M5.W8 (V33_OUT)
unnamed: J6.2, M5.W7 (SWCLK)
unnamed: J6.4, M5.W6 (SWDIO)
unnamed: J6.5, M5.W5 (nReset)
unnamed: J9.A5 (CC1), R7.2
unnamed: J9.B5 (CC2), R8.2
unnamed: M1.E6 (PG_5VP), R4.1
unnamed: M5.J1 (SEL1), M5.J_GND1 (PULL_DOWN1)
unnamed: M6.N14a (LED_GREEN), P4.1
unnamed: M6.N14b (LED_YELLOW), P3.1
unnamed: M6.E6 (SPI2_CS_/_CAN2_RX_(PB12)), M7.V6 (CAN_RX)
unnamed: M6.E7 (SPI2_SCK_/_CAN2_TX_(PB13)), M7.V5 (CAN_TX)
unnamed: M6.N14 (UART2_RX_(PD6)), P7.1, U5.1 (TXD)
unnamed: M6.N13 (UART2_TX_(PD5)), P8.1, U5.2 (RXD)
unnamed: Q7.1 (G), R17.1
unnamed: Q8.1 (G), R18.1
unnamed: Q9.1 (G), R19.1
unnamed: Q10.1 (G), R23.1
unnamed: Q11.1 (G), R24.1
unnamed: Q12.1 (G), R25.1
unnamed: C29.2, C30.2, D8.2 (K), L1.2, U4.3 (T+)
unnamed: C28.2, C29.1, D8.1 (K), L2.2, U4.2 (T-)

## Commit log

2026-01-02 uaefi 68pin
    [022035055.stp, 039301060.stp, 039301080.stp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]
2026-01-04 can2, egt, przesyniecie pcb
    [bom_replace_uaefi-e_.csv, uaefi.kicad_pcb]
2026-01-04 [skip actions] Auto-generated board v2.1
    [uaefi-B_Cu.gbl, uaefi-B_Mask.gbs, uaefi-B_Paste.gbp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]
